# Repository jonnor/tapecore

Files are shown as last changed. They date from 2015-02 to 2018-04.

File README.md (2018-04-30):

# TapeCore

Construction techniques for digital fabrication machines and linear axes that aim
to be extremely easy-to-replicate. Key ingredient is using tape surface for plain-bearings
on parts made with commonly available 3d-printers and/or laser-cutters.

# Handy

Open-bottom frame, meant to be positioned over workpiece/table.

## Handy A4

Small version, with A4 workarea (22 x 30 cm). 

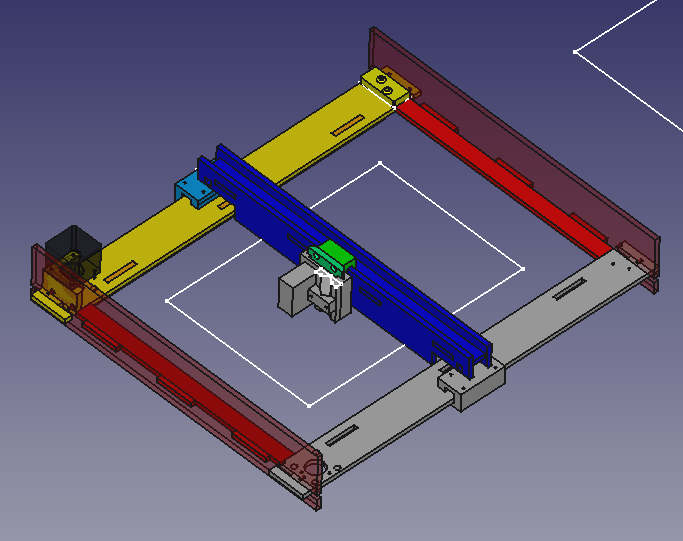
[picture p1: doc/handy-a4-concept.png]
TapeCore Handy A4


[FreeCAD project](./handy-a4.fcstd)

[Bill-of-materials](https://docs.google.com/spreadsheets/d/1o2K1h2c_w2d49ZTSx7vD1f-7HGYju6wTmgCQS48S1lg/edit?usp=sharing)

### Status
May 2018: **Needs revision**

Version 1 with split rails has a lot of backlash in the Y axis,
primarily due to the gantry twisting. This is planned fixed in a future version.

### Handy A4 penplotter

Firmware: [GRBL with servo](https://github.com/jonnor/grbl/tree/handy-a4-plotter).

CAM/MachineControl: Recommend [LaserWeb4](https://github.com/LaserWeb/LaserWeb4). Set gcode options, Tool On: `M3 S40` and Tool Off to `M3 S0`. 
Can also use Inkscape gcodetools + [custom postprocessor](./zservo_post.py) + Universal Gcode Sender

### TODO

v1.0 = penplotter

* Fix Y axis backlash. Use rail on each side?
* Improve diagonal stiffness. Wedge connecting rail with side?
* Add endstops
* Improve wire guides for motors
* Fix parametrics to respect material size+clearance
* Make pen pressure more even. Use a spring/rubberband in downward direction
* Publish files with part layout ready for lasercutting and 3d-printing
* Document assembly steps

v1.1

* Gantry: Avoid needing glue to assemble
* Gantry: Move adjustment of slider pressure to bottom. Wider sliders on top 
* Gantry: Move all wire attachment to front. Requires idlers/wires to be placed vertically
* Add wire guides to all idlers. Can be disassembled without loosing wires
* Add carrying holes to sides
* Add holes for attaching to table/wall

v2.0 = laserengraver

* Test running plotter vertically
* Test with laserhead, primarily engraving
* Add laser guard around diode (Rishalaser style)
* Add laser reducing light on sides+top, using window tinting film.
* Microswitch safety turns off laser if lifted from table

v3.0 = reprap?

* Test maximum cut depth in wood/plastic and 2.5w
* Test splitting gantry into 2/3 pieces

## Learnings

### Silicone good lubricant with Kapton
Pure silicone spray, like also used as mold release, is the best.
Works well with Kapton, gives good glide and seems to stay around for a while.
Mechanical lubricant spray based on silicone also works (tested manufacturer: WD40).
However is a bit too fluid, smells badly, and seems to dissolve glue of the Kapton tape.

### Mixing directions important with 3d-printed sliders

If parts are printed with sliding geometry in same direction they have same periodic pattern.
This becomes slightly 'interlocking' when sliding against eachother.
If one part is printed 90 degrees this locking effect does not happen.
Ex: If A is printed with sliding in X direction, print B with sliding in Z direction.

```
BAD
A:  | | |
B:   | | |

Good:
A: | | |
B: _ _ _
```

### Ideas

* 3d-print the 'dragchain' that guides wires etc out to toolhead.
Set of interlinking tubular pieces, possibly print-in-place.
Possibly held together by fishing line.

## Handy A2

Medium-sized machine, A2 workarea (60x42cm)

* Scaled up version of Handy A4 design
* Aim for 60x120 footprint or smaller. Can still fit on a typical table
* Splits gantry, sidewalls and rails into 2/3 pieces.

# Axi

Cantilevered CoreXY, inspired by Axidraw V3.
A4 workarea, for use with pen or laserhead.

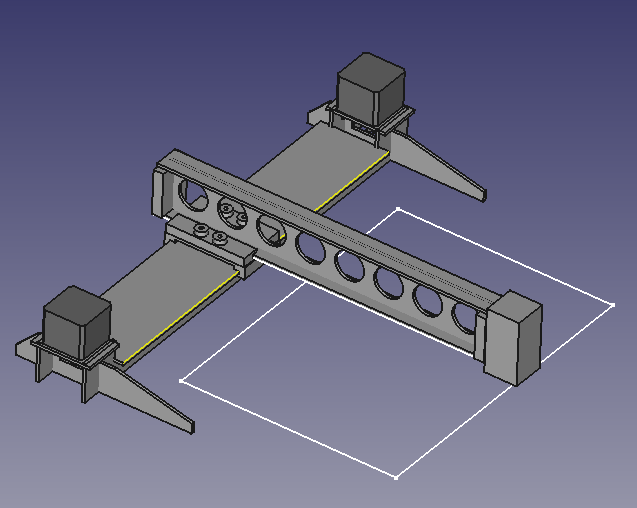
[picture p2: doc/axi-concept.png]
TapeCore Axi concept drawing


[FreeCAD sources](./axi.fcstd)

## Status
Just a concept sketch, not actively developed.

# Doverail Slim

First 3d-printed linear axis. Geometry inspired by dovetail slides found in lathes and mills,
and the narrow rail format inspired by Hiwin MDG type linear actuators.

[VIDEO: First tests](https://www.youtube.com/watch?v=5IGngfO671M)

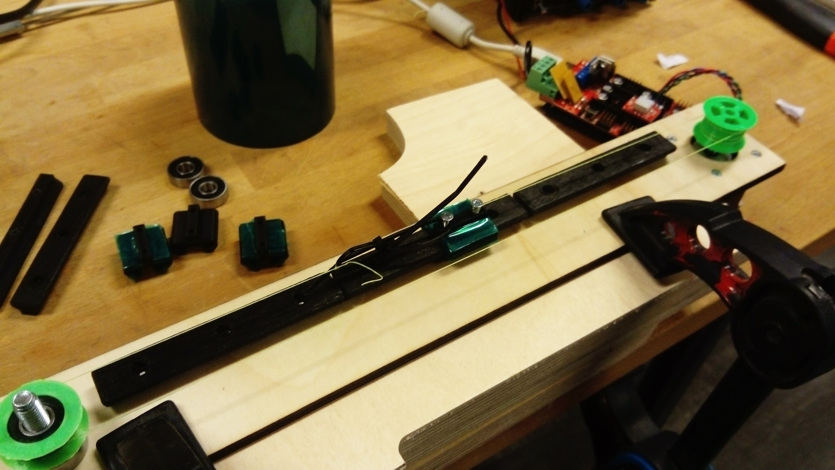
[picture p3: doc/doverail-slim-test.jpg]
Doverail Slim testing


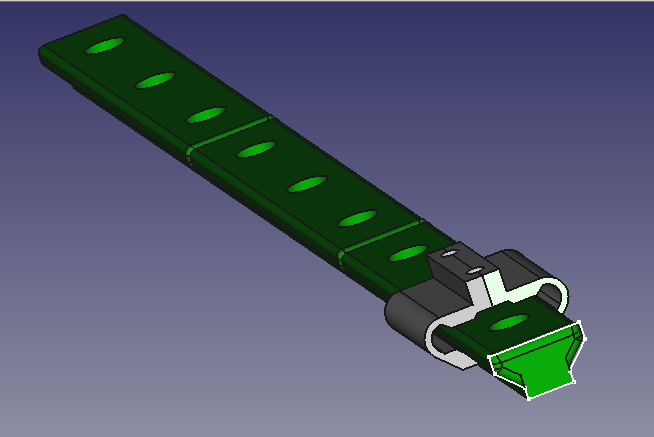
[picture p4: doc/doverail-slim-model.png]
Doverail Slim model


Flexing fingers on the slider gives some extra tolerance for variation along rail.
M3 screwholes for attaching to the support of the rail.
Multiple pieces can easily be joined together to build longer axes.

## Limitations

Side-loading capacity is limited due to springyness of slider fingers.
Rotational force will easily twist the slider.
The short slider length and narrow rail contributes, but also primarily due to flex of slider fingers.

So for a sliding Y bed (Prusa i3) would need dual rails.

Not suitable for cantilevered designs (Y axis on a PrintrBot Simple or Z-axis on Ultimaker).
It may be possible to compensate a little bit by using multiple widely-spaced sliders, as one would with a LMU6/8/10 based design.

## Learnings

### Tape adheres poorly to printed PLA
Poor adhesion of tape to printed PLA is a challenge.
Office-tape, Kapton and PET all stick pretty bad to the rough surfaces.
Especially for internal curvature. Applying tape to the rail is tricky due to its length, and while mounted together.
Having a precisely cut tape piece ahead of time would help, as would a mounting jig which still allows easy access to underside.

Edges to be taped should be: flat, tolerate slight misaligment and excess, ideally allow wrapping tape to adhere to itself.

### Vegetable oil gives higher static friction

When adding a couple of drops of olive oil to the PLA rail with PETP taped slider, the slider became much more 'sticky'.
Possible that sliding friction went down, but for plain bearing usually static friction is the biggest problem.
Wiping it off with a wet cloth fixed the problem.
Not known if a less viscous oil and/or hydrophobic/mineral oil would not have this problem.

### Sliding non-coated printed parts works

Since taping the rail is a bit tedious, we're primarily testing without any surface treatment on rail.
Against a PETP taped slider, friction is OK and there is no noticable wear after hundreds of repetitions.
Long-term wear is still unknown.

Not tested, but it looks like PLA against PLA may actually perform OK for very simple tasks with low load, low precision requirements.

This should be even better with a filament like PolyPropylene or Nylon,
which have a lower coefficient of friction and has self-lubricating properties.

## TODO

* Test the design on a Delta 3d-printer, or a CoreXY pen-plotter
* Make the FreeCAD properly parametric, with variables for length/height/width and tolerance 
* Change to 4x mounting holes on the slider, ideally compatible with MGN9
* Make an adjustable slider design that works

Contributions welcome!

# Doverail Wide

A redesign of the Doverail Slim to have a much wider rail (40-100 mm),
and using a slider which is fixed on one side and screw-ajustable tensioner on other side. 

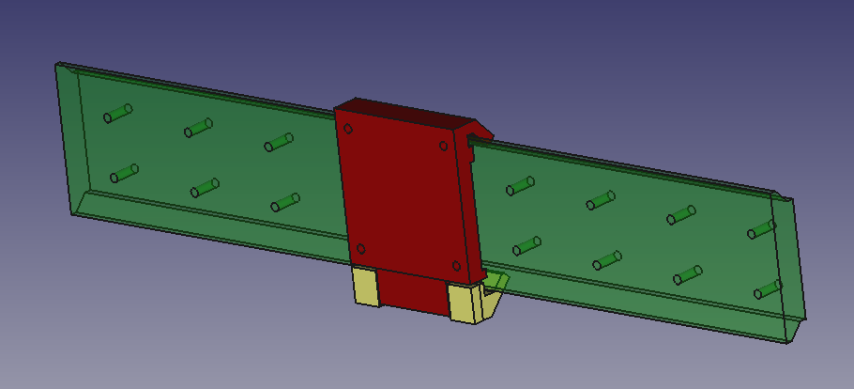
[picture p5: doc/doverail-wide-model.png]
Model of wide Doverail


This should significantly improve side-loading ability, and make suitable for more kinematic systems.
Examples would be an XYZ gantry-based system (as on many CNC-mills), and sliding-bed Y (like Prusa i3) using a single rail.
Even for a CoreXY laser or 3d-printer, the ability to have the X/Y rails vertical (like SmartRap Core)
simplifies how axes and end-effectors are attached.

Disadvantage is the higher material use and printing time.

## TODO

* Finish first model, print and test an axis
* Test with Kapton tape on slider, nothing on rail.
* Test with UHWM PE tape.
* Test on a vertical-rail X gantry, with end-effector
* Test on a sliding-Y bed

## Ideas

* Create sanding jigs, by adhering sandpaper to inner/outer shape, then slide one across the other.
* Use a steel rod as the idler instead of (608) bearing. For instance the head of a hex bolt?

## Tribology of common materials

Needed is some proper test procedure and data for coefficient-of-friction tests for commonly available materials and their combinations.

Examples:

* Candle wax. Polyurethane coating, epoxy coating.
* Lubricants: vegetable oil, sewing-machine-oil, mineral oil, silicone oil.
* Surface treatment: Sanding, heating, buffing

# TapeXY

Experiment in super low-cost XY stage, for uses in digital fabrication techniques
which have minimal weight and forces on head (laser engraving, 3d-printing).
Inspired by the [RishaLaser](http://rishalaser.org) project.

[Youtube VIDEO](https://www.youtube.com/watch?v=Eynk2ZyVWqM)

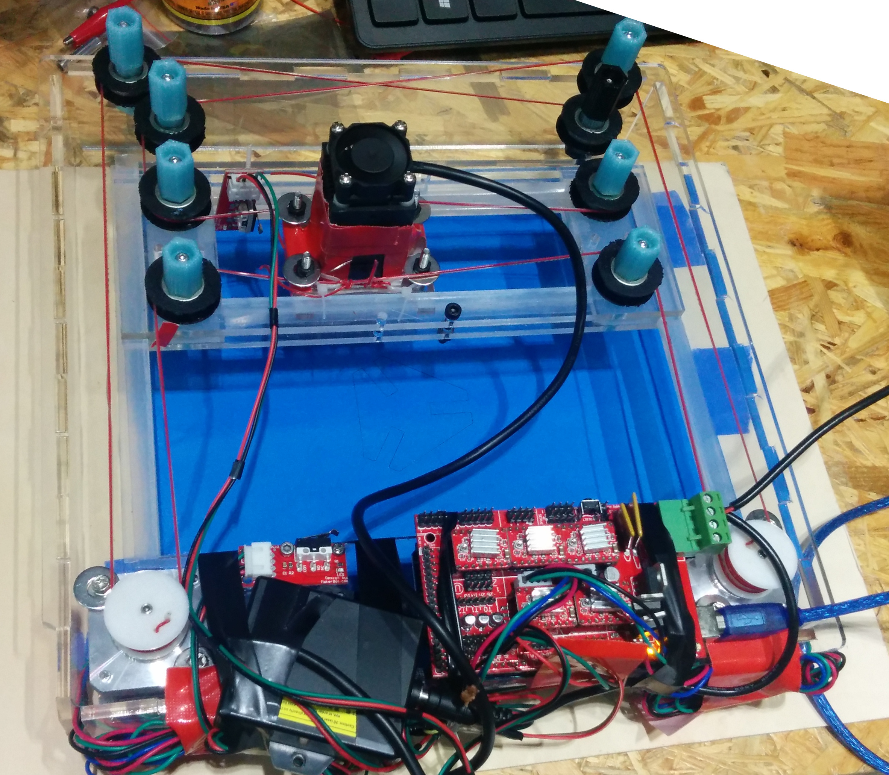
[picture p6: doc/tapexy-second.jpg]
TapeXY fully functioning prototype


Key features:

* Using low-friction tape as basis for gliding surfaces,
inspired by [a design](http://www.thingiverse.com/thing:3554) by Peter Jansen
* Using braided Nylon/Polyamid wire ("Spectra line") instead of timing belts.
Like on Tantillus and some Delta printers.
* Reproduction with primarily lasercutter (or CNC mill), in wood/acrylics.
* [CoreXY](http://corexy.com) kinematics

### Status
Not actively developed. Use [Handy](./README.md#Handy) instead

### Parts

Fabricated

* Frame [FreeCAD](./tapexy-frame.fcstd)
* Gantry [FreeCAD](./tapexy-gantry.fcstd)
* Head [FreeCAD](./tapexy-head.fcstd)
* Pulleys. NinjaFlex/SemiFlex for friction. [FreeCAD](./pulley-ninjaflex.fcstd)
* Idlers. 2x [sideguides](http://www.thingiverse.com/thing:31216) for 608 bearing

Assembly: [FreeCAD](./tapexy.fcstd)

Main vitamins

* MDF/Plywood/Acrylic 3-6 mm.
* 2x NEMA17 stepper motors.
* 1x Motion driver board. RAMPS or similar
* Cables for motors and endstops
* Low-friction tape, width at least 20mm. Recommened:
[UHMWPE 1in 3mil](https://www.amazon.com/JVCC-UHMW-PE-3-UHMW-Polyethylene-Film/dp/B00WUU61A) |
Alternative: Kapton tape, as used for Reprap 3d-printers.
* Strong line. Recommended: Braided fishing line (Spectra or similar).
Alternative: Nylon, Polyester or linen.
* 2x Endstops.

Misc vitamins

* 8x 608 bearings, for idlers.
* 8x M8x40 bolts, for idlers.
* 8x M3x10 bolts, for stepper.
* 4x M4x25 bolts, for head/gantry.

Effector

* 1x Laser diode module including driver.

## Done

* First working prototype of XY stage, driven by RAMPS/Cura
* [Laser diode driver](../currentsource). Linear constant-current source based on op-amp+MOSFET, for 5volt supply.
* Fully operational prototype, driven by RAMPS w/Marlin

### Limitations

* Non-standard lasermodule and attachment
* Gantry stiffness is too low
* Small working area, approx 15x10cm

Missing

* Holes in backwall for motor cables
* Mounting holes for endstops
* A belt/line attachment and tensioning system. Just use strip-ties??
* Holes for attaching RAMPS/controlboard
* Cables management for cables going to head/effector

## I-beam

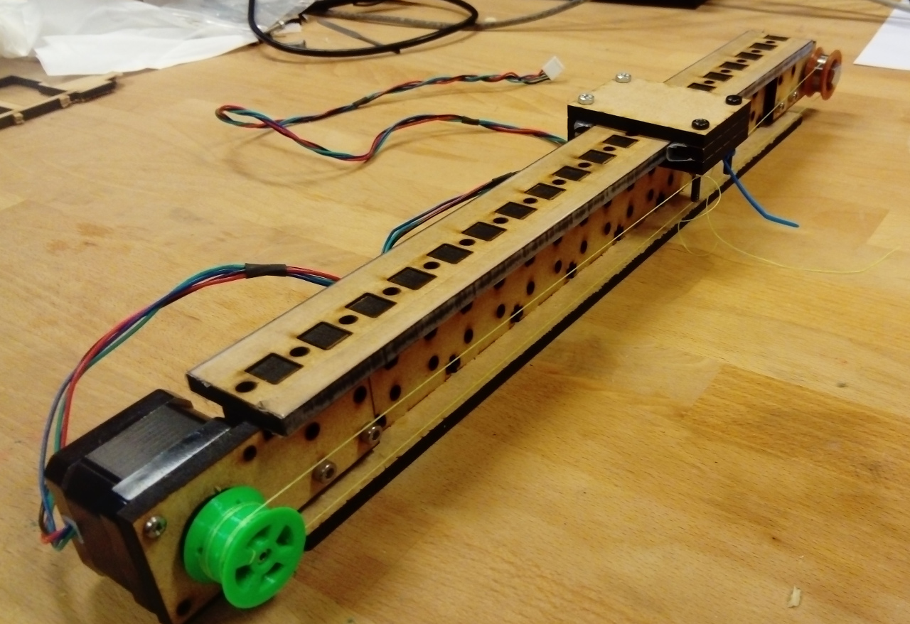
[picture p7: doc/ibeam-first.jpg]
First I-beam prototype


Designed to be a basic construction module, from which relatively large multi-axis machines can be made.

[v1 on Thingiverse](http://www.thingiverse.com/thing:1850612).
[v1 demo video](https://www.youtube.com/watch?v=oqJivOp4JyQ)

Features

* Rigid I-beam structure, with double-layer core for rotational stiffness
* Trapped nuts allows attaching from all sides
* Use as linear guide for slider by wrapping low-friction tape

Source files for FreeCAD

* [Beam](./ibeam2t.fcstd)
* [Slider](./ibeam2t-slider.fcstd)
* [Motor connection](./ibeam2t-motor.fcstd)

Vitamins needed:

* Low-friction tape. UHMW PE or Teflon ideal. Kapton also works OK
* NEMA17 stepper motor, incl M3 screws
* Braided line (fishing line or similar)
* 4 pieces M4x20+
* 4 pieces M4x15+

### TODO

Beam

* Improve trapped nut pattern in sides. Top-left and bottom-right (diagonal) should face one side
* Remove redundant (blind) holes in top/bottom layer
* Make tabs wider, reduce number by approx half
* Split up cut parts into multiple, with top/bottom/sides being a staggered/lapped
* Maybe reduce height/width a little bit. 30x40 mm?

Tests

* Test making axis in multiple parts, with total length 1.5-2x than machine working area.
* Test in 3-4 mm plywood. Faster to make and possibly self-replicatable. Is it rigid enough?
* Design & test a CoreXY using the I-beam as basic building block

Other designs for lasercut beams (untested)

* I-beam. [FreeCAD source](./ibeam-20.fcstd)
* II-beam. [FreeCAD source](./ibeam-30.fcstd)

Tools for calculating stiffness of beams

* http://www.had2know.com/technology/I-beam-calculator-moments-engineering.html
* http://www.engineersedge.com/section_properties_menu.shtml
* http://www.amesweb.info/SectionalPropertiesTabs/SectionalPropertiesIbeam.aspx
* https://en.m.wikipedia.org/wiki/Deflection_(engineering)
* https://en.m.wikipedia.org/wiki/List_of_second_moments_of_area

## CNC Z-axis

[Servo-driven Z-axis with ER11 shank driven by brushless motor](./cnchead.fcstd)

TODO

* Add rack&pinion
* Finish servo attachment
* Add holes for tightening screws for pen holding
* Test with pen
* Add pulleys
* Test with CNC spindle

Servo options. Should at least have 5 kg-cm

* [JX Servo PS-4806HB](https://www.banggood.com/JX-Servo-PS-4806HB-6KG-High-Torque-Standard-48_5g-Servo-for-RC-Models-p-1013373.html), 6kg-cm
* [TowerPro MG996R](https://www.banggood.com/TowerPro-MG996R-Metal-Gear-Digital-High-Torque-Servo-55g-p-982287.html), 10 kg-cm

## Pen Z-axis

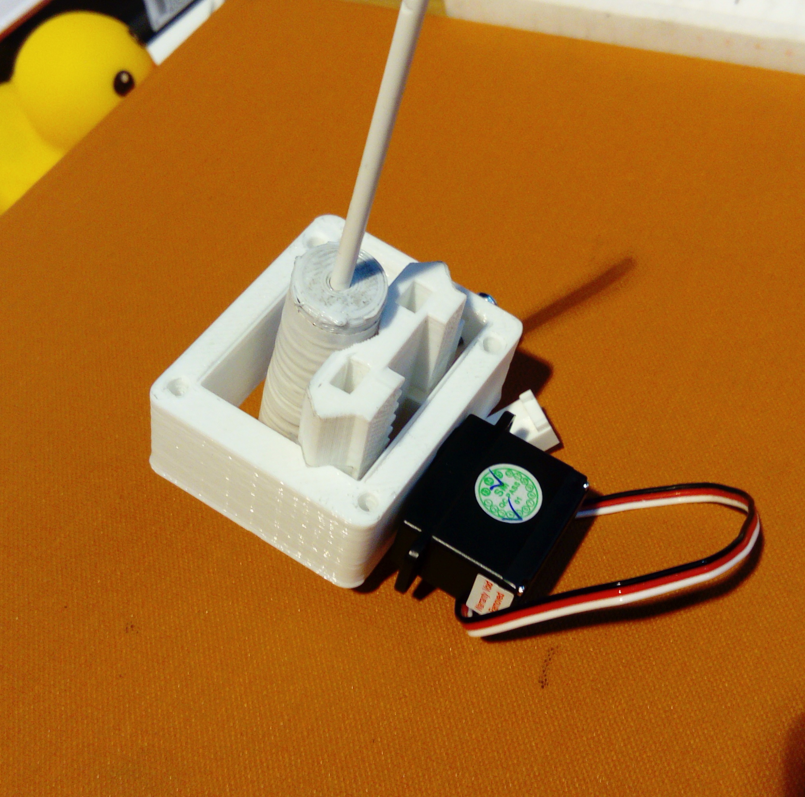
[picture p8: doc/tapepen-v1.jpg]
Servo driven Z axis for a pen holder


3d-printed files [on Thingiverse](http://www.thingiverse.com/thing:1850720).
[FreeCAD source project](./tapepen.fcstd).

Using a printed V-rail geometry, covered with low-friction tape.
Has adjustment for the tension, was very practical to dial in the correct amount.

Fits pens 8-15 mm in diameter.
Lifts straight up, perpendicular to surface. Roughly 10 mm travel.
Unlike many others servo-driven pen axes which rotate when lifting pen. 

Used in the penplotter which was the award given to the winners of Oslo Innovation Award 2016.
Successfully printed the diploma live on stage.

Vitamins needed:

* Microservo. SG92R or other with same size head, https://www.adafruit.com/product/169
* Low-friction tape. UHMW PE or Teflon ideal. Kapton can be used as replacement
* 2x M3x30 + M3 hex nuts for attaching pen to slider
* 2x M3x30 for adjusting tension on the slider

TODO/improvements

* Use a slightly bigger/stronger servomotor
* Use as basis for a lens-moving Z axis for lasers.
Probably use 3 v-rails instead of 2, keep tensioning principle.

Existing designs by others

* Servo+fishingline, spring in one direction. http://www.thingiverse.com/thing:749118
* Servo with 2-bar linkage, lasercut. http://www.thingiverse.com/thing:4185
* Servo with PTFE bushing, spring in down direction. http://www.thingiverse.com/thing:13407
* Servo with rotating slot linkage, lasercut+3dprint. http://fab.cba.mit.edu/classes/863.14/people/nathan_melenbrink/Week_15.html
* Servo with steel bars and POM bushing parts. CNCed https://www.tindie.com/products/ijinstruments/servo-actuated-pen-slide/
* XY pan+tilt mover, with Z motion. http://www.thingiverse.com/thing:31463

## Wallmounted 3d-printer

Concept based on TapeXY mechanics, adding a wire-driven cantilevered Z-axis.

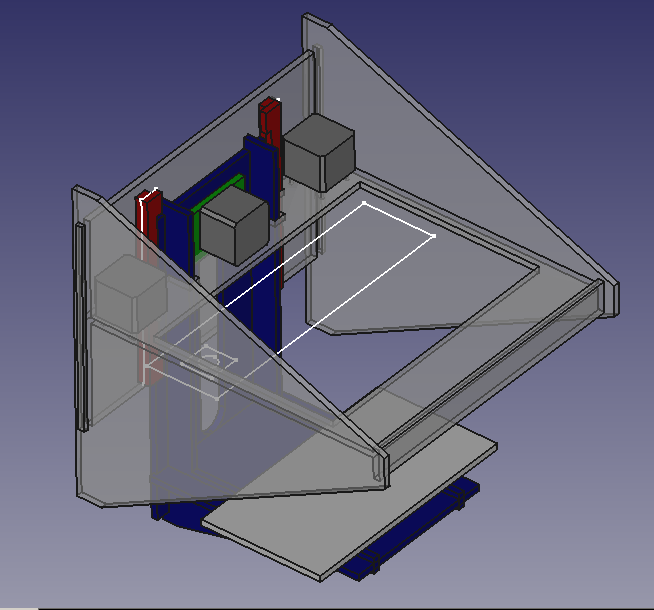
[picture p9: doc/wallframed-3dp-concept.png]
Wall-mounted 3d-printer

[FreeCAD project](./wallframed2.fcstd)

Designed for mounting on a wall, to keep precious desktop space untouched.
Inspired by machines such as the SmartRap Core.

## Reproducability

### Power needed to reproduce itself.

Mr.Beam II says that with 5W they can cut 4 mm plywood in two passes (no focus adjustment).
It seems to be a blue diode laser with no air assist. This probably sets 5W as the a lower limit.

* Adding air-assist might improve cutting efficiency a bit.
* Adjusting the focus into the material for each pass might help
* Using PWM to overdrive the laser periodically may also help

If one could cut 4 mm acrylic instead, or 5-6 mm plywood, that would make it simpler to make a more rigid machine.
This _might_ be doable with 8-10 watts IR diode. If more is needed, may need to assemble 15-20 watt using multiple diodes.

[8W diode laser cutting 4mm plywood single pass](https://www.youtube.com/watch?v=gWxxxrpdF10)
[5.5W laser cutting 4mm plywood single pass](https://www.youtube.com/watch?v=fT6_FLB4vyM)
[3.5W laser cutting 3mm acrylic single pass](https://www.youtube.com/watch?v=rqom-Ns8LqA)
[3.5W laser cutting 3mm plywood 5 passes 12mm/s](https://www.youtube.com/watch?v=iQ14XSbGCJk)
[5.5W laser cutting 3mm plywood 2 passes](https://www.youtube.com/watch?v=j0H8-iMtKs4)

### Construction tricks

To make more reproducible

* Use I/H beam or similar structures to achieve stiffness
* Use 2x 2-3mm material instead of 1x 4-6mm, sandwiched using interlocking geometry.

General best practices

* Use same bearings and screws types everywhere

Self-reproducability.

* Need to create structure bigger than own working area.
Let I/II-beams consist of multiple sections, with staggered joints?
Do testing of a long beam (50 cm+). Flatness, stiffness, maximum load.
Keep compatible with alu profiles? T-slot/Makerbeam/Openbeam

## Laser diodes

* Bangood [1.6W](http://www.banggood.com/Wholesale-Laser-Equipment-c-3491.html),
[3.5W](https://www.banggood.com/450nm-3500mW-3_5W-Blue-Laser-Module-With-TTL-Modulation-for-DIY-Laser-Cutter-Engraver-p-1103261.html),
[5.5W](http://www.banggood.com/445nm-5_5W-5500mW-Blue-Laser-Module-With-Heatsink-For-DIY-Laser-Cutter-Engraver-p-999283.html)
[7W](https://www.banggood.com/EleksMaker-LA03-7000-445nm-7000mW-Blue-Laser-Module-With-Heatsink-For-DIY-Laser-Engraver-Machine-p-1127310.html),
[15W](https://www.banggood.com/445-450nm-15W-Blue-Laser-Module-Mark-On-Metal-for-DIY-Laser-Engraver-Machine-p-1137779.html)

* Osram PL TB450B [DigiKey](http://www.digikey.com/product-detail/en/osram-opto-semiconductors-inc/PL%20TB450B/PL%20TB450B-ND/5719266)
* [DTR's Laser Shop](https://sites.google.com/site/dtrlpf/home/diodes)
* [Laserdirect@Ebay](http://www.ebay.com/sch/laserdirect/m.html?_nkw&_armrs=1&_ipg&_from&rt=nc&_mPrRngCbx=1)

Fibre guided

* [Ebay: 8 watt NIR 980nm](http://www.ebay.com/itm/980nm-8W-Fiber-Coupled-Laser-Semiconductor-Fiber-Coupled-laser-8000mW-IR-Laser-/141524214275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)
* Ebay: [3W](http://www.ebay.com/itm/Laser-Diode-3-1-Watt-923nm-Fiber-Coupled-100um-JDSU-6380-L2-3-1W-NEW-63-00123-/111598682682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)
and [5W](http://www.ebay.com/itm/Laser-Diode-5-Watt-915nm-Fiber-Coupled-100um-JDSU-6390-L3-5W-NEW-63-00192-/111598671030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)

Should be possible to [combine](https://www.rp-photonics.com/beam_combining.html) multiple such fibre laser diodes with one focusing lens (maybe with colliminator).
To achieve powers of N times the individual laser source. Though with simple combinators, the brightness will not increase so much, due to widening of beam size.
 Also the heatsink no longer needs to be on the head, reducing weight of moving parts.

## CO2 lasers

For cheap lasercutters, CO2 lasers are used.

There are several aspects which are challenging.

* Laser tube itself
* Cooling the gas
* The optics
* Power supply

Principle

Using gas mixture of helium, nitrogen, and carbon dioxide gas.
A common standard mixture is 4.5 percent CO2, 13.5 percent N2, and 82 percent He. Penn suggests using a mixture of 14:14:72 in narrow-bore CO2 laser.

Aactive cooling to keep the temperature of the discharge tube below around 30 degrees C or so.

Flowing-gas lasers

"the flowing-gas CO2 laser requires a vacuum pump to achieve the low pressures (10-30 torr or so)"

* [35 Watt Flowing Gas CO2 Laser Tube Kit](http://repairfaq.cis.upenn.edu/sam/rconway/35wtkit.pdf), assembly instructions.
* [Flowing gas CO2 laser conversion from sealed gas](https://www.photonlexicon.com/forums/showthread.php/17719-Flowing-gas-CO2-laser-conversion-from-sealed-gas)
* [First Homemade CO2 Laser Built From Scratch](http://jarrodkinsey.org/co2laser/co2laser.html)

References

* [Understanding CO2 laser](http://www.laserk.com/newsletters/whiteCO.html)
* [RP Photonics Encyclopedia: CO2 lasers](https://www.rp-photonics.com/co2_lasers.html), describes different types. Sealed tube versus
* [Homebrew CO2 Laser Design and Construction Notes](http://www.timefracture.org/laserdocs/laser_design_notes.html)
* [RepairFAQ: Home-Built Carbon Dioxide (CO2) Laser](http://www.repairfaq.org/sam/lasercc2.htm). Looots of information
* [RepairFAQ: Carbon Dioxide Lasers](http://www.repairfaq.org/sam/laserco2.htm). Loots of information

## Related projects...

Of mine

* [Clothing](../clothing), various techniques rely on laser
* [Rishalaser](../rishalaser), build of existing open-source low-powered laserengraver

Existing low-cost laser diode engravers

* [smartDIYs](http://www.thingiverse.com/thing:1026345) open source kit. Lasercut acrylic, steelrods+timingbelts, motor on gantry.
* [Mr. Beam](https://www.mr-beam.org/) open source kit. Kickstarter 2014. 3d-printed + wood-frame. [Octoprint-based](https://github.com/mrbeam/OctoPrint) software
* [Emblaser](https://darklylabs.com/emblaser-overview) [2](https://sites.google.com/site/3dprinterlist/lasercutters/darklylabs-a3-diode-laser)
* [Fabool Laser Mini](http://www.smartdiys.cc/fabool-laser-mini/) claims to be openn source. Also has a CO2 laser available.

Other inspirational machines

* [MPlus One](http://www.thingiverse.com/thing:1104249).
Cantilevered, moving bed like PrinterBot Simple and Smartrap, with lasered/milled structure.
Maybe has potential in combination with tape principle, possibly making even cheaper than a CoreXY?
* Axidraw V3
* Cloth of the Bot

Possible addons

* [Lasercut vacuum table](http://hackaday.com/2016/03/19/diy-vacuum-table-makes-lasering-even-easier)
* [Air assist for diode laser](http://www.thingiverse.com/thing:1688209), 3d-printed using a radial fan
* [Air assist for compressor](http://www.thingiverse.com/thing:72691).
Seems a small oil-free compressor (airbrush etc) is good enough. Recommened ratings are 30-50 PSI at 1-2.5 CFM.

## TapeZ

Moving-bed Z-axis stage for laserengraver/3d-printer to go with TapeXY.
Also uses Kapton tape and braided Nylon wire.

Existing wire/belt Z-axis:

* [SmartRapCore alternative Z](http://www.thingiverse.com/thing:896556)
* [Sli3dr](http://richrap.blogspot.co.uk/2014/07/3d-printers-big-printers-small-printers.html)
* [Igentis](https://www.youmagine.com/designs/ingentis-a-tantillus-variant)
* [Printxel](http://printxel.blogspot.ca/2012/12/printxel-community.html)
* http://forums.reprap.org/read.php?177,310249
* http://forums.reprap.org/read.php?160,170024
* http://forums.reprap.org/read.php?177,192178
* http://forums.reprap.org/read.php?14,319321
* http://forums.reprap.org/read.php?279,188149

A challenge is that Z-resolution/precision might be a bit low without gearing.
The hold-torque of a NEMA17 stepper might also not be enough to keep bed up.
Reduction gearing of between 1/4 and 1/9 is desirable.

## TapeCrane

My dad wants to build a cheap, large-scale 3d-printer (workspace with sides of 50-100cm)
which could be stowed away when not in used. For this he had two ideas for the kinematics.
One being a robot arm with two joints (elbow and wrist), working in the XY plane. Like SCARA.
The arm up/down or the bed would move to form Z axis.
The effector is cantilevered, making it tricky to keep rigid, and there are multiple
solutions for the inverse kinematics and singularity points.

The other idea was more like a crane, a [cylindrical robot](https://www.google.no/search?q=cylindrical+robot&tbm=isch).
It has the advantages of much simpler inverse kinematics (because no articulated joints),
and that the structure can be made more rigid in various ways:
Using tensioned wires (like a guy-wire), by supporting the far end, and/or using a (moving) counterbalance.

The most common configuration, has a rotating base. Alternatively, one can rotate just the (elevated) arm.
Either the whole arm can move back & forth to move end-effector, or the effector can travel along a static arm.

Unlike a cartesian or delta robot, several cylindrial robots could work into the same workarea.
They could potentially collaborate on a single (large) part, either for speed or multi-filament.
Or indepentently making different parts, or multiple instances of the same part.

Example of multi-arm collaborations

* Flexible + rigid printing
* 3d-printing binder + laying out fiber threads
* Rough 3d-printing + precision lasering/milling
* Conductive + non-conductive 3d-printing

Challenges:

* Having enough resolution in rotating joint. Probably will need gearing, challenge then becomes low/zero backlash in gear
* Mimizing angular momentum of rotating joint, for maximum speed / minimum force. Keeping weight down, and it close to center of axis
* Cylindrical sectioned build area, does not fit typical objects well. Can partition the circle into 3/4/6/8 rectangular build areas
* Decreasing precision at long-reach. Can also be seen as feature, better precision on small objects

TODO:

* Sketch a rough concept
* Test an arm beam, with tensioned wires on top+bottom for ridigity
* Implementing the IK for cylindrical in firmware

# Experiments

## PlateXY
Experiment in extremely simple plotter/laserengraver.

Features

* Head is wire-suspended between fixed rails (no gantry),
* Glideblocks tensioned by the drive wires
* Custom rails fixed to standard plate

### Status
**Aborted**. In favor of [Handy](./README.md#Handy)

The gantry-free design was found not good enough for penplotting use.
The lack of locking between the two sliders meant they would move independently, causing a twist in the head.
At A4 size it might have been barely acceptable, but not better than simpler kinematics like [Axi](./README.md#Axi).

However this kinematics can be useful when precision is not needed, and it is desirable to hide the mechanics of the machine.
For instance with the rails mounted to floor/ceiling, and using transparent fishing line, one can make pieces move around in XZ 'invisibly'.

## Kapton 608 bearing

.. Wednesday 14 Oct 2015, Oslo ..

Attempted to create a 608-sized bearing/bushing. 3d-printed, using Kapton tape added afterwards.
Using a V-profile to make the bearing support some axial load.
Initially 120 deg, but had to increase to 135-degrees to make it possible to insert inner part into outer ring.
Tolerances when 3d-printed (on a Ultimaker Original) seemed generally OK.

However, major issues were found when trying to assemble.
The Kapton tape was not particularly sticky to the print,
and would not easily fold around the V-profiles, especially the outer ring (with inward V profile).
When pressing the inner part of the bearing in, would easily
move the carefully aligned tape... Avoiding folds/creases was quite tricky.

I was able to succesfully assemble one bearing, with tape only on the inner part.
This rotated quite nicely, with not too much play.
Considering the application of belt pulley, where some excentricity is quite OK.
Indicates that if one can figure out a practical assembly, the idea has some merit.

It could be that in larger scale, and with a more adhesive tape and, or with simpler geometry,
that the idea would have some merit. But with v-style 608 the process was too fiddly to be practical.

For TapeXY it could be possible to design an alternative idler/pulley solution.
For instance one could integrate the belt bottom/top guides, and use top/bottom of
rotating part for supporting the (tiny) axial load.

It is however desirable to be compatible with a standard solution,
or at least also allow a standard solution - since a hacked thing will (probably?)
never be as good as a proper bearing.

TODO

* Test cutting low-friction tape to revolved V-shape using laser.
If necessary, try to use additional glue. A jig for pressing the tape against when adhering could also help?
* Try an inverted design: inward V on inner part, outward V on outer ring.
This should be easier to adhere tape to, as the ring has shape towards the top/bottom, not hidden inside.
* Test using UHMW PE / PTFE tape.
* Design an integrated bearing+belt idler for CoreXY usage, compatible with 608-based

## References

Work by others

* [3d-printed bushing](http://www.thingiverse.com/thing:1196801), replaces speciality linear bearings
* [3d-printed beam surface](http://www.thingiverse.com/thing:9080/#comments)

General machine building

* [Methods for minimizing gear backlash](http://machinedesign.com/motion-control/methods-minimize-gear-backlash),
spring-loaded distance, spring-loaded split gears, backloading/dual-gear-train
* [3d=printed anti-backlash gear](http://www.thingiverse.com/thing:98393), dual layer with printed integrated springs.

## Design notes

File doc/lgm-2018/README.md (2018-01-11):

# LGM2018 workshop

* Where: Seville, Spain
* When: April 26-28
* Status: Proposed

http://libregraphicsmeeting.org/2018/

## Title
Plotting openly 

## Proposal
Before the ubiquity of inkjet printers and mobile devices, the pen-plotter was a common way to physically realize and share a digital drawing. Today the plotter remains one of the simplest example of a computer-controlled fabrication device, perfect for learning the basics of digital fabrication.

Join us to learn how these machines work, how to control it using open software and make them output your drawings!

We will provide some plotters based on the TapeCore open hardware project. The machines are designed to be easily replicated in a local makerspace/fablab, so that you can build your own.

Participants should bring their laptops.

## Presenter bio
Jon is an engineer who loves working on projects which combine software, electronics and mechanics.
Since 2016 he is active in the maker community in Oslo, researching how make digital fabrication
accessible by designing open-hardware machines that require a minimum amount of specialized parts and skills.

Jon has previously participated in the libre graphics community as a MyPaint and GEGL/GIMP developer.
At day he runs an Internet-of-Things consultancy named Flowhub.

## TODO

Machine

* See ./README.md

Workshop

* Decide format/structure
* What software should participants use/learn?

Maybe

* Test laser-engraver head
* Test dragknife head

## Goal
Finish first version of simple plotter/engraver.
Documentation enough to replicate locally.
Inspire others to replicate it in their local lab.

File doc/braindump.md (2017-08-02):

# Endstops and autoleveling probe

Endstops are cheap, but a specialized part. It would be great if we could reproduce them.
Using a conductive filament (like ProtoPasta Conductive), one could create traces which
can be connected together. In PLA one could design a spring which would separate the traces.

TODO: 

* Do research of existing work on reprappable endstops/switches
* Do reserch on suitable spring designs
* Design and print a prototype
* Test repeatability

On a 3d-printer could use mechanical switches/endstops as an autoleveling probe.
The problem however is that the switch cannot be lower than the nozzle when running
- it will interfere with printing.

* Have an endstop on two sides of the nozzle, some millimeters higher than nozzle
* Each corner of the build plate, has an elevated area (a bit).
* When running autoleveling, head moves such that the switch is above each of the areas before moving down.
* The hit-targets in the corners can also be the clamps for the glass-plate
* Note: requires careful calibration of build size area
* If repping endstops is cheap enough, can be achieved easily using min+max stops.
* Another advantage is that one can use a printed piece with correct offset
to autolevel also ontop of objects (like a CNC mill)

# Coating 

Using coats of an epoxy-like binder as an alternative to tape.
Can both provide structural stength, binding individual parts and getting a slick/hard sliding surface

* [How to measure friction](http://www.tribology-abc.com/abc/friction.htm)
* [Understanding Polyurethane Friction](https://www.slideshare.net/SunrayInc/understanding-polyurethane-coefficient-of-friction).
Harder -> lower friction.
Wet Polyurethane COF `<0.3` against stainless steel, and `<0.7` when dry.
Wood against dry Polyurethane `<0.2` for 75D hardness.
* [Testing coating hardness using pencil method](http://www.woodweb.com/knowledge_base/Testing_Your_Coatings_Hardness.html)
* Durometer. [1](https://www.amazon.com/MegaBrand-Durometer-Digital-Hardness-Tester/dp/B011JCG1KK)

# Reprappable laser

Using Rishalaser/TapeXY as a base.
Focusing first on ultra-low cost for use with textiles & paper,
with long-term goal of having high enough power to cut itself and similar structures.

## Milestone 1: Simplified mechanics (DONE)

* CoreXY architecture.
* Using string (Nylon) instead of belts
* Tape (Kapton/Scotch) slide-bearings
* See [TapeXY](../README.md#TapeXY)

## Milestone 2: Raster firmware (in progress)

* Couple open source alternatives available

## Milestone 3: 

* CNC-millable PCB with discrete H-bridges & microcontroller
* Firmware runs directly on this microcontroller

## Milestone 4: Fabbable motors

* Either brusless with gearing and closed-loop, or a direct-drive stepper
* 3d-printed or lasercut bobbins and structure
* Etched

## Milestone 5: Custom CO2 laser tubes

* See [Kreatures work](http://hackaday.com/2015/09/13/building-a-3d-printed-laser-tube/)
* If one can get them up to 20+ watt, should be able to reproduce

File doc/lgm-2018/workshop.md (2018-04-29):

## Tapecore @ LGM2017 - Plotting along openly

https://github.com/jonnor/tapecore

## Goals
- Understand the TapeCore project.
Motivation, construction principles, current state
- Understand basics of digital fabrication.

## Non-goals
- Learn to build machine

## Format

1. Demo
2. Talk, some background
3. Hands-on usage

## About me

Contract

    Twitter: @jononor
    Github: jonnor
    Web: https:/jonnor.com

Background

    BEng. Electronics 
    Software Engineer: Embedded, Open Source
    (ex) Bike mechanic

    Libre Graphics 2009-2014. MyPaint,OpenRaster,
    Maker community. 2014-< . Bitraf & Fellesverkstedet
    
Dayjob

    Independent consultant. Internet of Things. Rapid prototyping. SW/E.eng/M.Eng 
    MSc. Data Science. Machine learning

## TapeCore

- LOW cost
- LOW tech
- OK performance. Sub-millimeter precision

Fabricatable in makerspace/fablab 

- Few speciality tools
Lasercut + 3d-printed.
- Few speciality parts.
Instead: Digital fabricated and generic consumables.
Tape (Kapton/UHWMPE), Wire/fishing line.

### Handy A4

Designed in FreeCAD

[Bill of Materials](
https://docs.google.com/spreadsheets/d/1o2K1h2c_w2d49ZTSx7vD1f-7HGYju6wTmgCQS48S1lg)

Why penplotters

GRBL controller
https://github.com/gnea/grbl

## Review

Good

- Portable
- Open bottom frame

Needs work

- Backlash in Y axis. Replace split rail with individual rails 
- Glue needed for gantry slider.
- Diagonal stiffness too low
- Too many screws

## Fabricatable machines

https://github.com/fellesverkstedet/fabricatable-machines

- Medium to high-end machines
- CNCed Aluminum/POM
- Chamfer rail
- Humprey: Full-size CNC
- FAB2.0 - build a Fablab in a Fablab

## Digital fabrication

### Concept

    Digital 3d-model + digitally controlled fabrication machine
    => automated production of
       software-defined physical objects

In practice:

- Manual labor needed.
Postprocessing, machine tending
- Craft involved.
Design-for-manufacturing, technology choice, choosing machine parameters

### Where is this taking us?

- Less human labor needed
Cheaper products. Fewer jobs
- Less manual skills needed
Beginners can get good results also.
- Mass-production
Automated, easy to scale up
- Mass-customization
Each part can be unique 

### Democratization

Ensure the benefits are widely distributed instead of going to a selected few.

* Shared public access.
Maker/hackerspaces, Fablabs
* Open online manufacturing services.
Ponoko,3d-hubs,Shapeways,iMaterialize
* Open source hardware.
Reprap project, Prusa i3
* Open source software.
 Grbl, Marlin
* Consumer market.
Low prices, OK volume.
Makers as early adopters

### Process

Generally

    CAD -> CAM -> MC

    CAD: Computer-Aided Design
    CAM: Computer-aided Manufacturing
    MC: Machine Control

Example Plotting:

    Inkscape -> Inkscape gcodetools -> OctoPrint 

Example LaserCutting:

    FreeCAD -> AutoLaser -> Control panel on Redsail

Example generative code

    Python script generates

Why these divisions?

- Legacy: In instrustry often separate personell for each role
- CAD: Best software depends on what to design.
- CAM/MC: Depends on technology

### Languages

https://www.shapeoko.com/wiki/index.php/G-Code
http://reprap.org/wiki/G-code

Alternative for penplotters: HPGL

```
PU100,100
PD200,200
```
Often in 1/64th inch etc

## Machine

Open loop. Dead reckoning

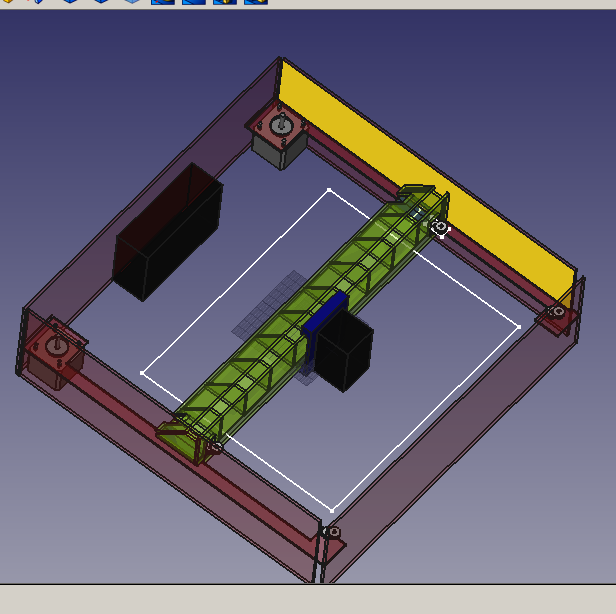
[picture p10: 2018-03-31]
doc/corexy3-concept.png

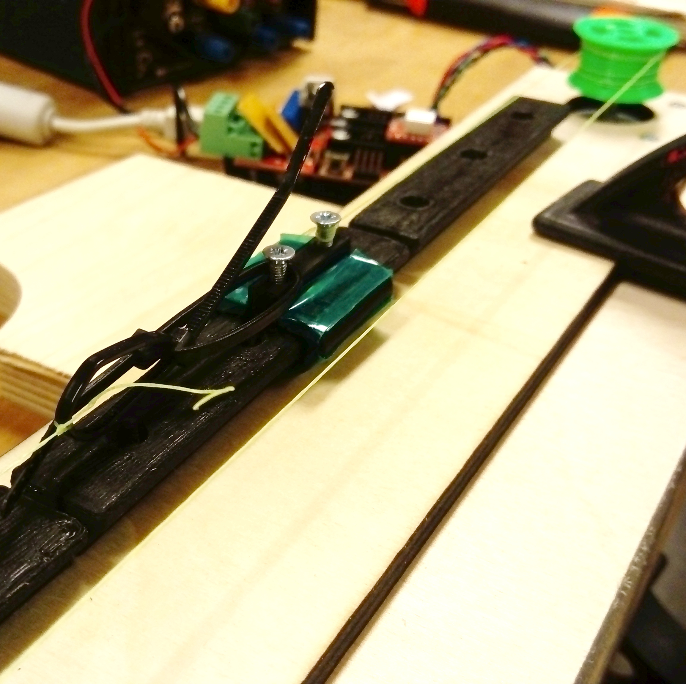
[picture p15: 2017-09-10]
doc/doverail-slim-square.jpg

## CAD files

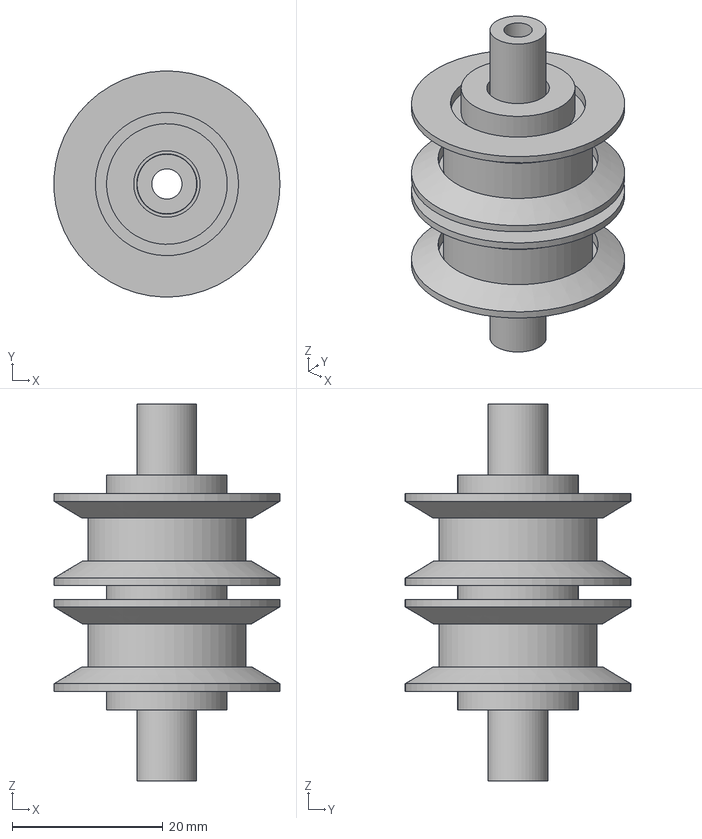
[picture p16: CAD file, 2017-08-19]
tapexy-bearing-assembly-x2.fcstd
30.0 x 30.0 x 50.0 mm
spacer

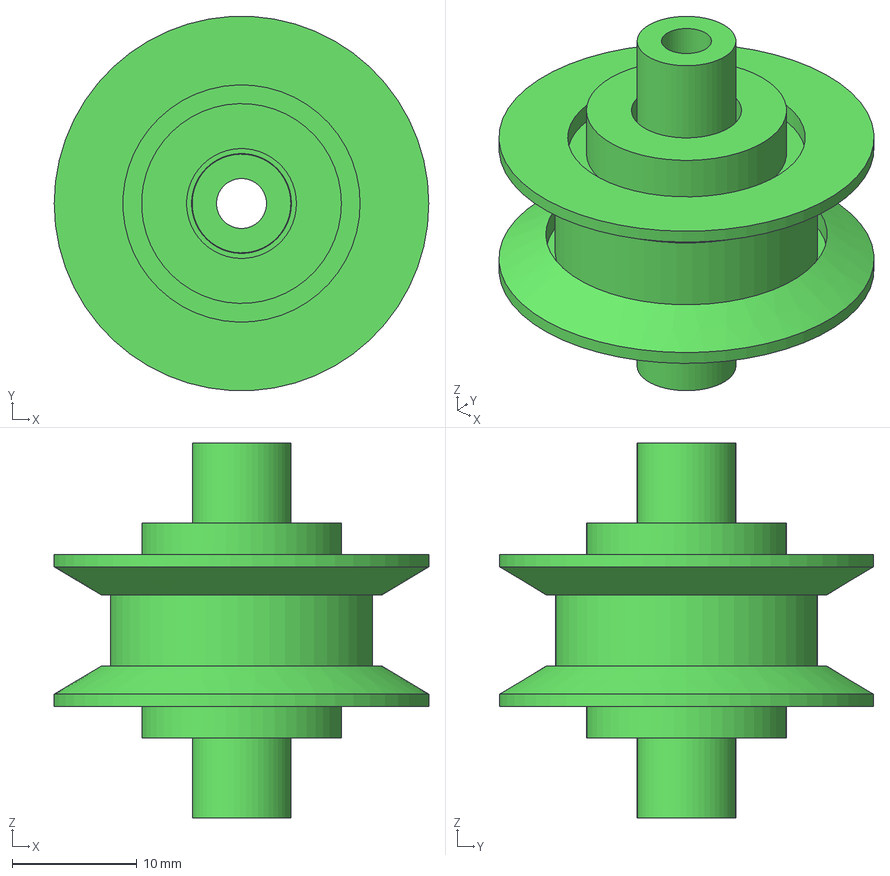
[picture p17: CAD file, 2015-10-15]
tapexy-bearing-assembly.fcstd
30.0 x 29.9 x 30.0 mm

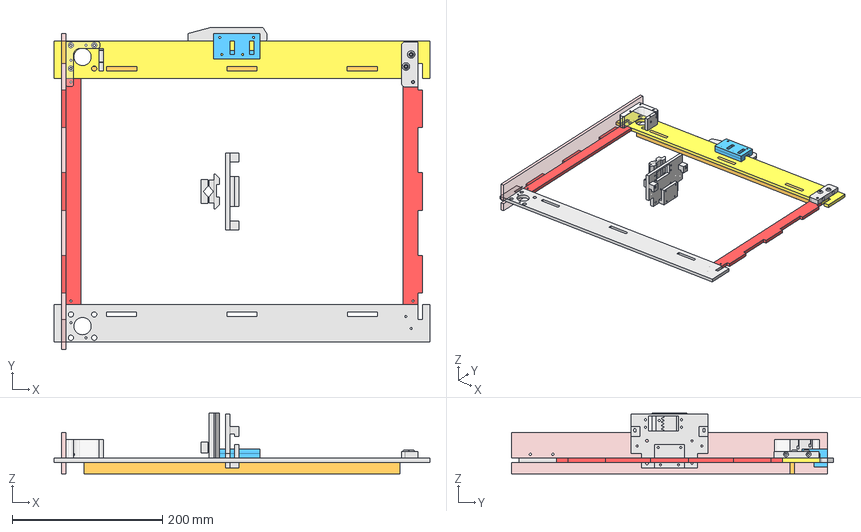
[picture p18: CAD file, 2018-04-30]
handy-a4.fcstd
500.0 x 428.0 x 81.1 mm
slider-left
rail-right
rail-left
front-stiffener
side-front
back-stiffener
motoroff

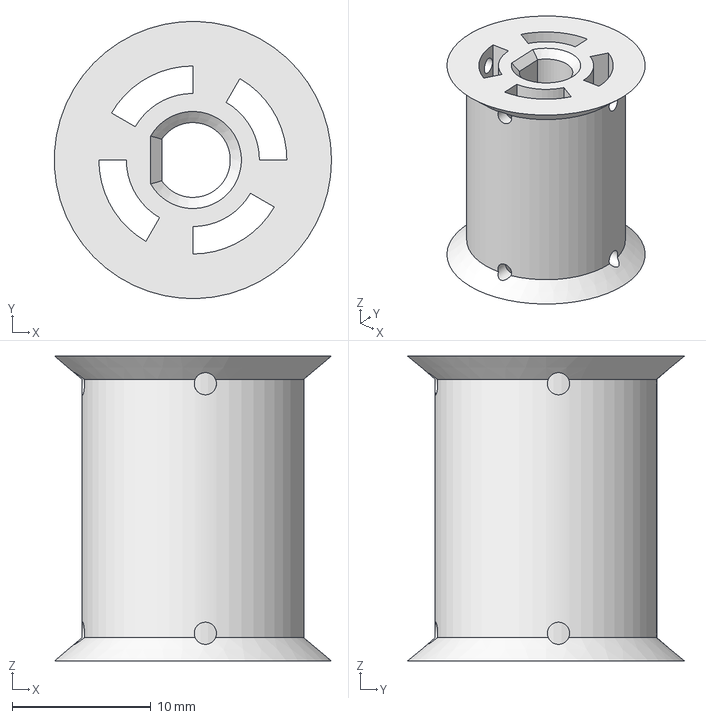
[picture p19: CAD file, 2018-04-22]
pulley.fcstd
20.0 x 20.0 x 22.0 mm

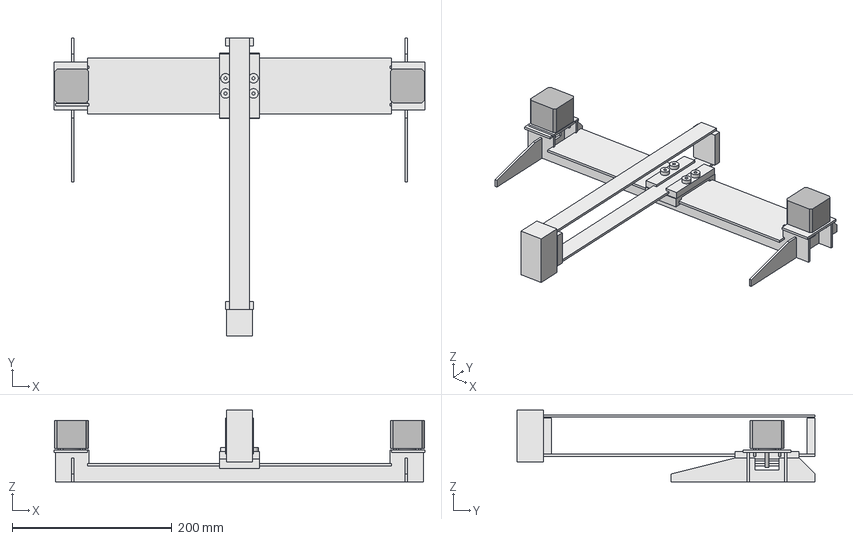
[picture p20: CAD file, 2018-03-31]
axi.fcstd
464.0 x 373.0 x 90.0 mm
nema17-wscrews[step]
Pad (Mirror #1)
Pad007 (Mirror #5)
nema17-wscrews[step] (Mirror #2)
arm-top
Pad005 (Mirror #3)
Pad006 (Mirror #4)

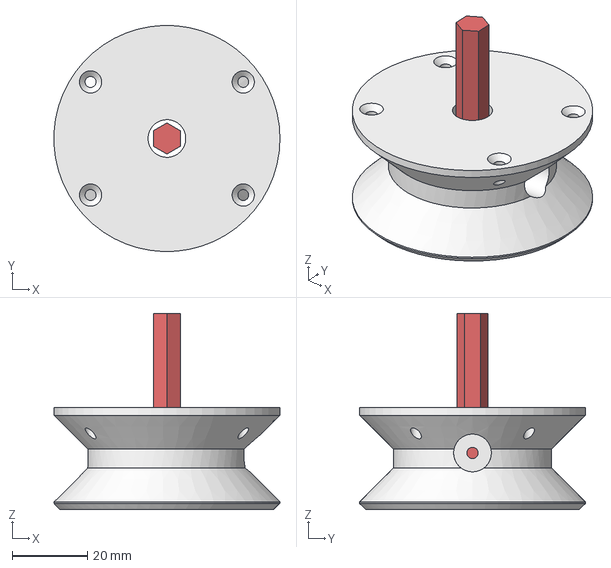
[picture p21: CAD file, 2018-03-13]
penheadhack.fcstd
60.0 x 60.0 x 52.0 mm

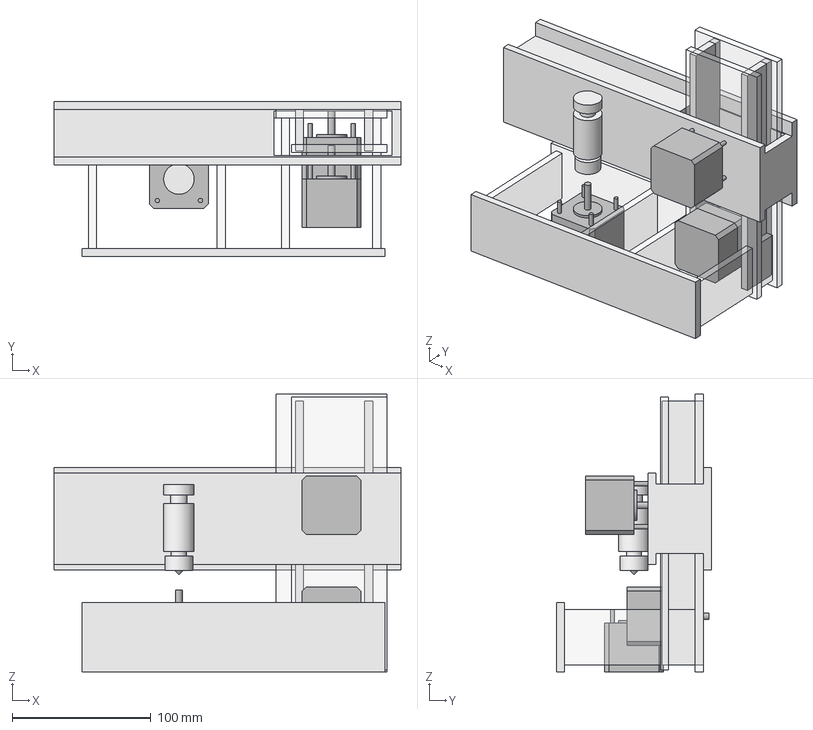
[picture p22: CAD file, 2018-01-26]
cantilever-3d.fcstd
250.0 x 112.0 x 200.0 mm
x-motor
y-motor
z-motor

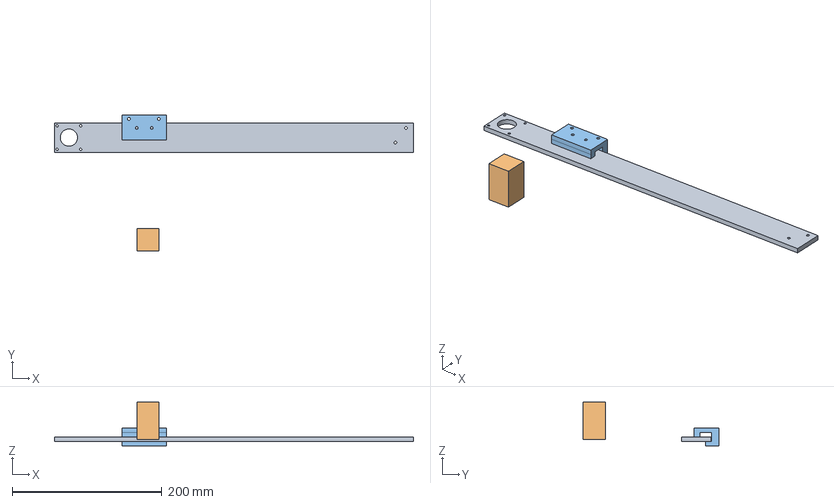
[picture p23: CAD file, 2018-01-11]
platexy.fcstd
480.0 x 181.5 x 58.6 mm
rail

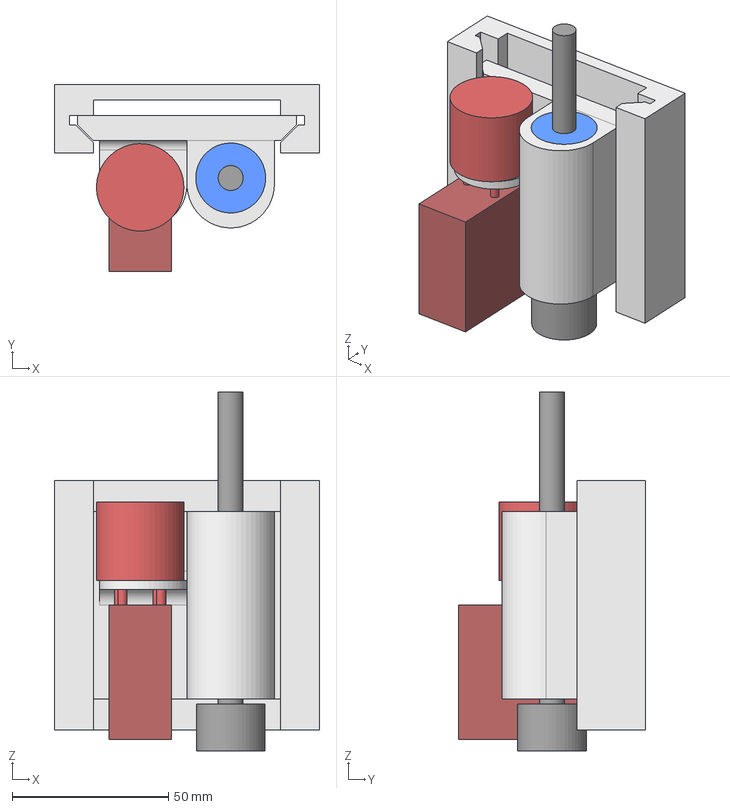
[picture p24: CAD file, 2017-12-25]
cnchead.fcstd
85.0 x 60.0 x 115.0 mm
bearings
axel
Mirrored
motor

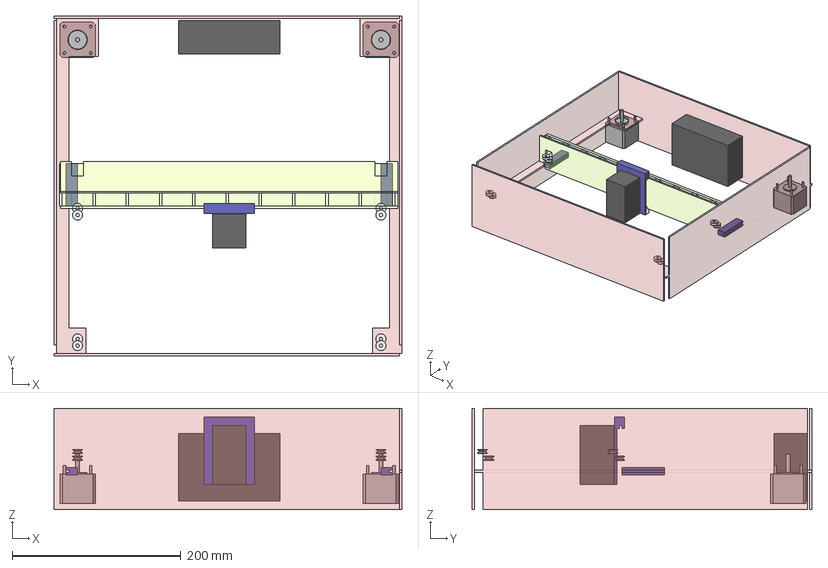
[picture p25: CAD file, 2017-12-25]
corexy3.fcstd
413.0 x 403.0 x 120.0 mm
frame
Pad009 (Mirror #4)
gantry
nema17-wscrews[step]
nema17-wscrews[step] (Mirror #7)
bearings
Clone of bearings

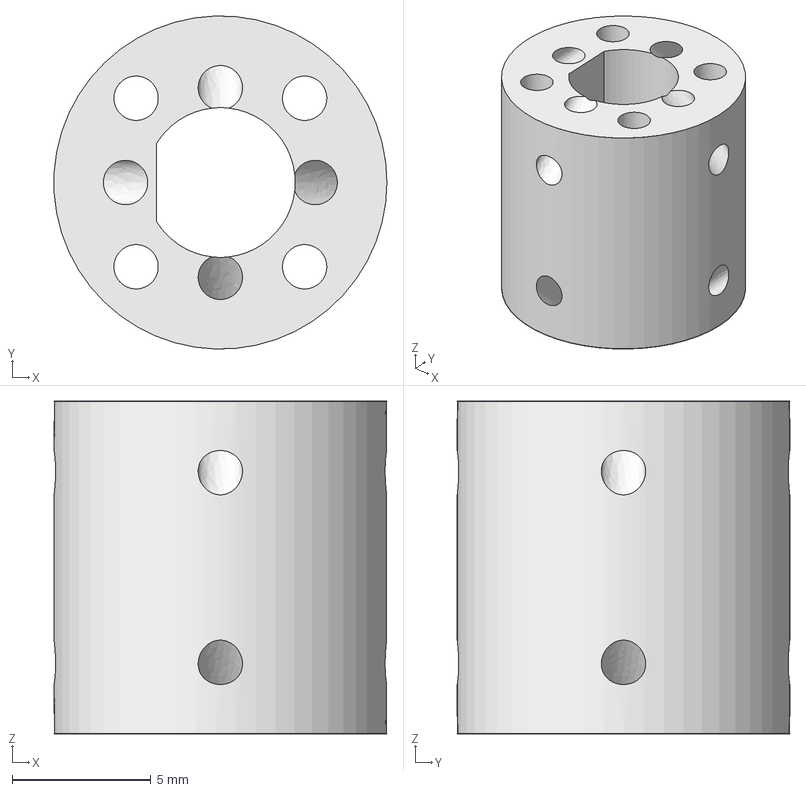
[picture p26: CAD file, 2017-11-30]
pulleysmall.fcstd
12.0 x 12.0 x 12.0 mm

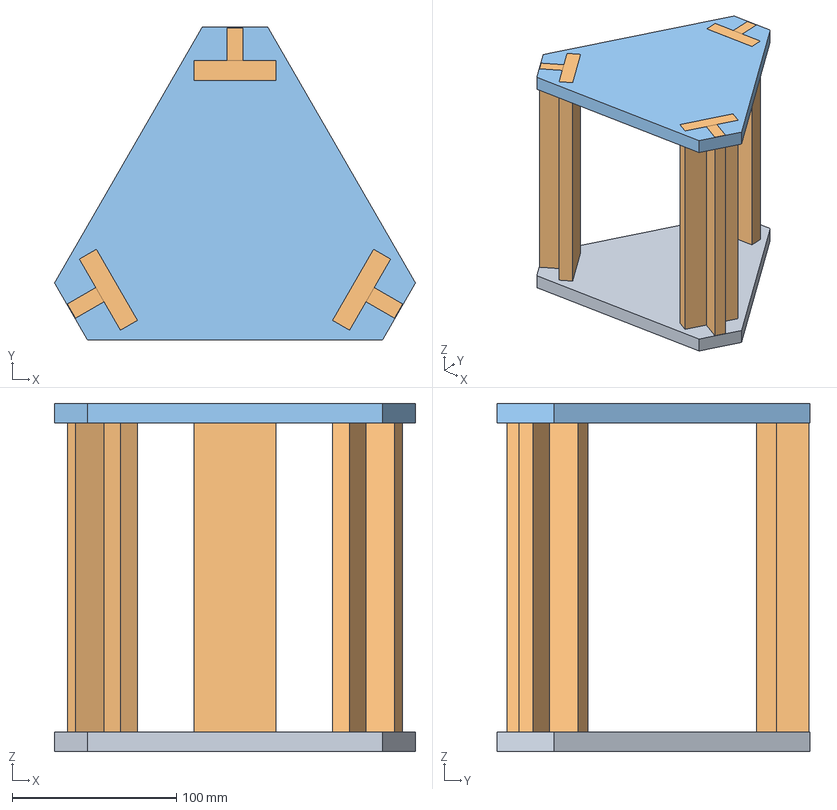
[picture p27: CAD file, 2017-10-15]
delta.fcstd
219.8 x 190.4 x 212.0 mm
Clone of Pad

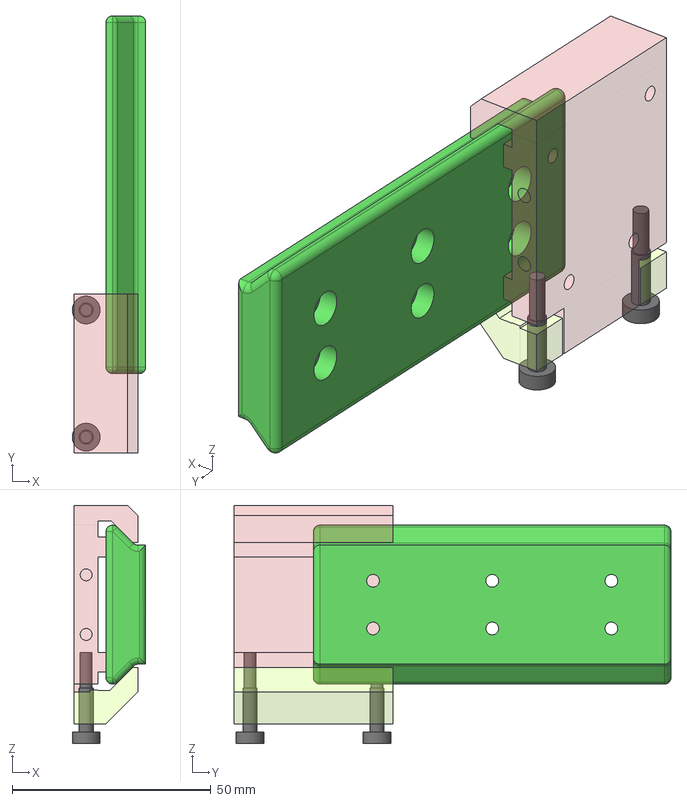
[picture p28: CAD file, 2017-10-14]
doverail-wide.fcstd
18.5 x 110.0 x 60.0 mm
Cut[stl]
slider-screw

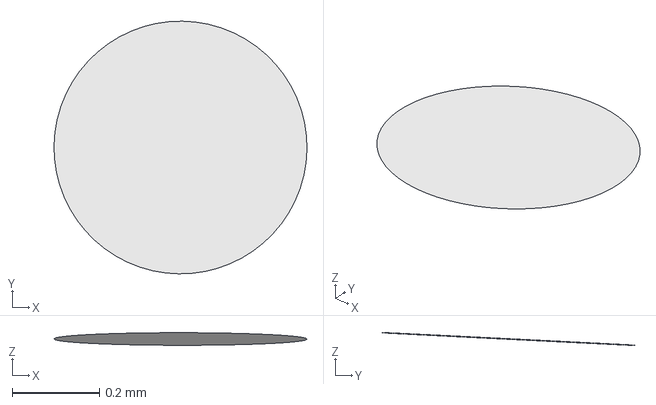
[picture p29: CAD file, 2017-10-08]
cycloid.fcstd
0.58 x 0.579 x 0.029 mm

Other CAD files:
gantry-adjuster.fcstd
doverail-slim-slider-adjustable.fcstd
doverail-slim.fcstd
tapecorexy2.fcstd
bearingadapter-10mm.fcstd
ibeam-20.fcstd
ibeam-slider.fcstd
ibeam2t-motor.fcstd
ibeam2t.fcstd
idlerwheel-30deg.fcstd
iibeam-30.fcstd
limitswitch-holder.fcstd
m8alt.fcstd
nema17-standoff.fcstd
nema17.fcstd
penspring.fcstd
pulley-ninjaflex.fcstd
tape-slide.fcstd
tape608ov.fcstd
tapecore-3d.fcstd
tapecrane.fcstd
tapepen.fcstd
tapexy-frame.fcstd
tapexy-gantry.fcstd
tapexy-head.fcstd
tapexy-kapton608.fcstd
tapexy-kapton608v.fcstd
tapexy.fcstd
tapez-bed.fcstd
tapez-frame.fcstd
tapez.fcstd
tolerancetest.fcstd
vrail-inner.fcstd
vrail.fcstd
wallframed-zadjuster.fcstd
wallframed.fcstd
wallframed2.fcstd

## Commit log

2015-02-27 reprapping: Add flex joint and stepper motor model
    [28byj-48.fcstd, flex-rod-coupler.fcstd]
2015-02-28 reprapping: Add step export of stepper motor
    [28byj-48.step]
2015-03-01 reprapping: Add idler wheel, 30 degrees
    [idlerwheel-30deg.fcstd, idlerwheel-30deg.step, idlerwheel-30deg.stl]
2015-03-05 reprapping: Add NinjaFlex based head for deltaprinter
    [ninja-deltahead.fcstd, ninja-deltahead.stl]
2015-09-18 reprapping: Initial linear actuator based on Kapton tape
    [tape-slide.fcstd]
2015-09-18 reprapping: Tape slide linear stage with NEMA17
    [tape-slide.fcstd]
2015-09-19 reprapping: Working version of tapeslide
    [pulley-ninjaflex.fcstd, tape-slide.fcstd]
2015-09-20 reprapping: Initial TapeXY test
    [tapexy-gantry.fcstd, tapexy.fcstd]
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2015-09-28 reprapping: Add idea about using Kaptop for direct bearings (608 size)
    [tapexy-kapton608.fcstd, tapexy-kapton608v.fcstd]
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2015-10-15 tapexy: Use Assembly2, Mmove head and frame into dedicated files
    [tapexy-frame.fcstd, tapexy-gantry.fcstd, tapexy-head.fcstd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]
2015-10-15 tapexy: Add initial bearing assembly
    [tapexy-bearing-assembly.fcstd, tapexy.fcstd]
2015-10-15 tapexy: Make belt be in one plane, add steppers to assembly
    [nema17.fcstd, tapexy-frame.fcstd, tapexy-gantry.fcstd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]
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2015-10-28 reprapping: Initial TapeZ design
    [tapez-bed.fcstd, tapez-frame.fcstd, tapez.fcstd]
2015-10-28 tapez: Add joinery to bed model
    [tapez-bed.fcstd, tapez.fcstd]
2015-11-02 tapexy: Double-layer gantry, downscale to 150x105 mm
    Stiffer gantry, should also be scaleable upwards by also
    adding plates vertically to form a H/I beam type structure.
    Easier/less wasteful to prototype at a smaller size.
    [tapexy-frame.fcstd, tapexy-gantry.fcstd, tapexy-head.fcstd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]
2015-11-02 tapez: Only lock against side of plates, adjust for 150x100mm build
    [tapez-bed.fcstd, tapez-frame.fcstd, tapez.fcstd]
2015-11-02 tapecore-3d: 3d-printer concept from TapeXY + TapeZ
    [tapecore-3d.fcstd]
2015-12-20 reprapping: Add some robot-arm sketches
    [parm-arm.fcstd, parm-bot.fcstd, parm-horizontalbearing.fcstd]
2015-12-20 reprapping: parm minimalize bearing holder
    [parm-horizontalbearing.fcstd]
2015-12-20 reprapping: parm, chamfer horizontal bearing holder
    [parm-horizontalbearing.fcstd]
2015-12-20 reprapping: Add a test receiver for parm
    [parm-receiver.fcstd]
2015-12-22 reprapping: Update arm with rounding etc
    [parm-arm.fcstd]
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2015-12-30 tapexy: Add sketch for flex/spring hole for gantry
    [tapexy-gantry.fcstd]
2015-12-30 reprapping: Add a generic 20x20 I-beam, designed for laser/CNC
    4mm (or adapt for 3mm) material
    [ibeam-20.fcstd]
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2015-12-31 reprapping: Fix bug in mid-holes of II-beam
    [iibeam-30.fcstd]
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2016-02-05 reprapping: Update head with springing and less touch-areas
    [tapexy-head.fcstd]
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2016-05-06 reprapping: Initial M8 bolt replacement
    [m8alt.fcstd]
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2016-05-09 reprapping: Fix hole too narrow for M8 bolt alternative
    [m8alt.fcstd]
2016-06-30 reprapping: Add another v-bearing design for 3d-print+tape liner
    [tape608ov.fcstd]
2016-07-01 reprapping: Add tape geometry for V bearing
    Somehow unable to unroll it though...
    [tape608ov.fcstd]
2016-07-10 reprapping: Add a limitswich mount/holder design, for lasercutting
    [limitswitch-holder.fcstd]
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2016-07-16 tape608: Slightly looser to accomodate tape, chamfer for printability
    [tape608ov.fcstd]
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2016-08-01 tapexy: Minor updates for gantry+head for testing v2
    [tapexy-gantry.fcstd, tapexy-head.fcstd]
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2016-08-10 Add a tolerance test file
    [tolerancetest.fcstd]
2016-08-11 Add some adapters for using 10mm ID bearing
    [bearingadapter-10mm.fcstd]
2016-08-11 Fab12 fabricated head, without flexing holes
    [tapexy-head.fcstd]
2016-08-26 Add start of a servo-actuated penholder
    Needs to add servoattachment+rack,
    and tune to better fit in the lasermodule envelope
    [tapepen.fcstd]
2016-08-27 Penholder, basic mechanics completed
    Missing rack+pinion and servo mounting
    [tapepen.fcstd]
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2016-10-11 penspring: For mounting a ballpoint ink cartridge with spring tensioning
    [penspring.fcstd]
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2016-10-13 tapepen: Tweaked tolerances, tested by hand working
    [tapepen.fcstd]
2016-10-13 tapepen: Add rack+pinion, increase width, add adapter plate
    [tapepen.fcstd]
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2016-10-16 tapepen: Make whole thing fit inside 31mm vertically
    [tapepen.fcstd]
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2016-10-21 pulley: Add pulley with openings for anchoring wire
    [pulley.fcstd]
2016-10-26 README: Major update with I-beam and pen Z axis
    [ibeam-slider.fcstd]
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2016-10-27 README: Add link to nice anti-backlash gear
2016-11-11 Add some sketches for a printed/CNCed supported vrail
    [vrail-inner.fcstd, vrail.fcstd]
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2017-08-18 wallframed: Initial gantry design
    Using vertically mounted bearings
    Motor placement probably need to be wider still though
    [wallframed2.fcstd]
2017-08-18 wallframed: Update width, initial belt paths
    Motors will need offset plates, possibly with cutouts for belt
    [wallframed2.fcstd]
2017-08-19 Add two-level CoreXY design
    Vertically layered bearings, and square-beam profile gantry
    with end-effector mounted on the front (conventional)
    This design should be able to scale up to very large machines
    [tapecorexy2.fcstd, tapexy-bearing-assembly-x2.fcstd]
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2017-09-10 doverail: Move flex slider into main file for slim rail
    [doverail-slim-slider-adjustable.fcstd, doverail-slim.fcstd, doverail.fcstd]
2017-09-10 pulley: Fix idler sides, was missing hole
    [pulley.fcstd]
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2017-10-14 doverail: Redesign for 40mm
    [doverail-wide.fcstd]
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2017-11-22 pulley: Back to big one, calculate error due to height difference
    [pulley.fcstd]
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2017-12-23 Sketch for integrated CNC head
    With servo on head, rack&pinion drivesys
    Designed for 3dprinting
    Especially for light loads such as milling PCBs
    [cnchead.fcstd]
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2017-12-25 cnchead: Most parts in place
    Missing rack & pinion
    [cnchead.fcstd]
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2018-01-26 cantilever-3d: Add concept sketch
    Roughly the kinemantics used on Wanhao i3 mini
    and similar low-end printers.
    For workareas of 10-12cm cubed
    [cantilever-3d.fcstd]
2018-03-11 Add nogantry, next iteration of platexy concept
    * Open frame bottom
    * Much wider bearing spacer on slider
    * M3 everywhere
    [nogantry-a4.fcstd, penheadhack.fcstd]
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2018-03-29 Fix missing holes for motor corner bracket
    [nogantry-a4.fcstd]
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2018-03-30 Rename nogantry to Handy
    Since it has a gantry now...
    [handy-a4.fcstd]
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2018-04-17 handy: Start of new slider
    Servo will be on top of gantry slider instead of zaxis
    Height of gantry reduced a bit
    [handy-a4.fcstd]
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2018-04-21 handy: Add holes in side stiffeners
    [handy-a4.fcstd]
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2018-04-22 handy: Add a rough guide for wires going into pulley
    [handy-a4.fcstd]
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
